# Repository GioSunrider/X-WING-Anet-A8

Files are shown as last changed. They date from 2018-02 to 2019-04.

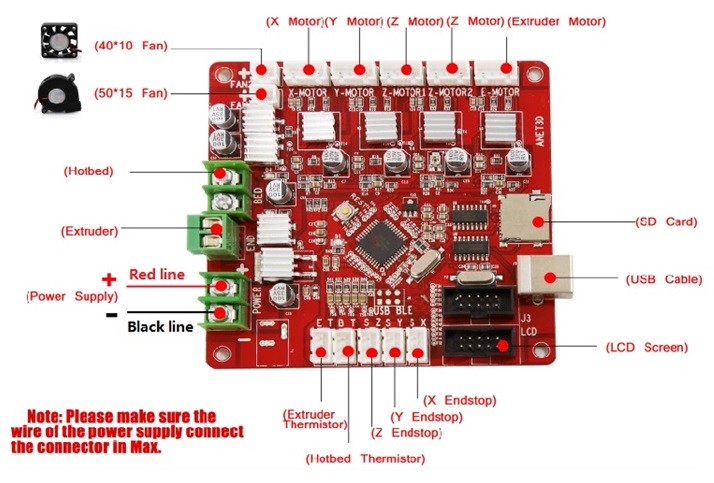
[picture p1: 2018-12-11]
English Instructions/Tool List&other pictures/Mainboard-English.jpg

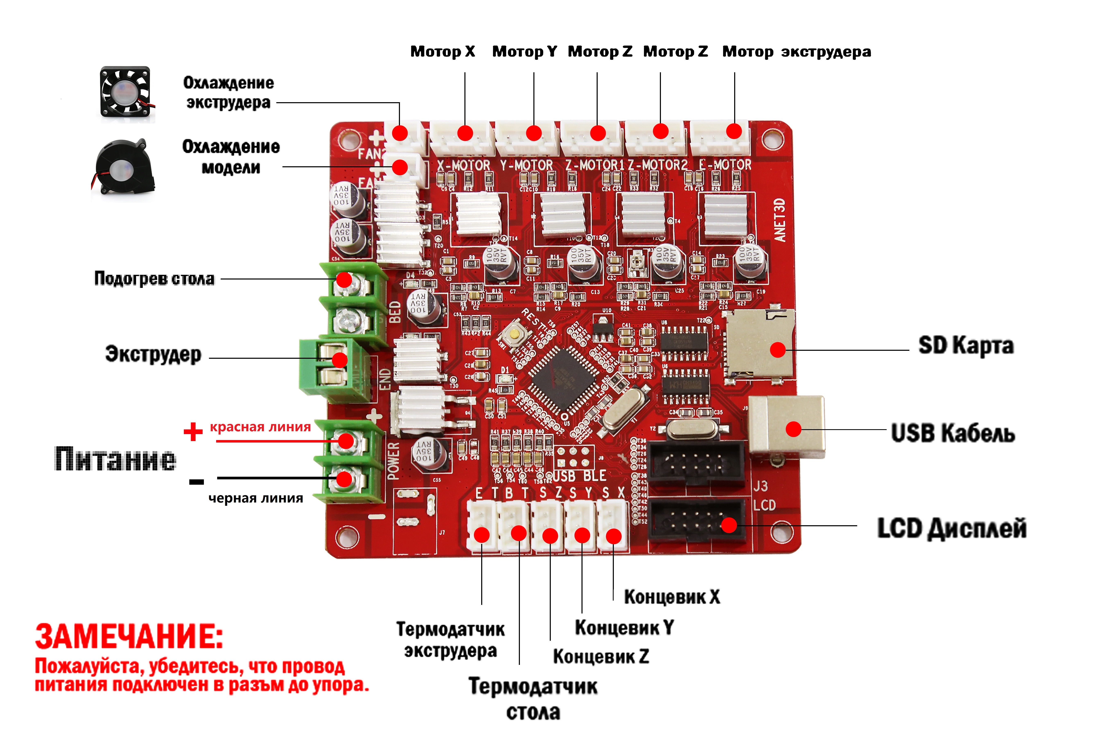
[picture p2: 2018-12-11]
English Instructions/Tool List&other pictures/Mainboard-Russian.jpg

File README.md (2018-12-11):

# X-WING Anet-A8
Proyecto de mejora y documentación de una Anet A8 bautizada como X-WING

En este repositorio se colgara todo lo necesario para su mantenimiento
y mejora de la misma. Asi como sus posibles archivos de configuracion.
______________________________________________________________________________________________

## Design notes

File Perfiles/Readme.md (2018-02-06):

En esta carpeta se encuentran los perfiles de Simplify3D que
se utilizaran en la impresora X-Wing.

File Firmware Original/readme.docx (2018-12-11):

第一步(step 1)

解压avrdudess.zip 文件（ unzip the avrdudess.zip file）

第二步(step 2)

Open avrdudess>avrdudess.exe

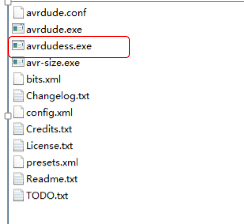
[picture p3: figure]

第三步(step 3)

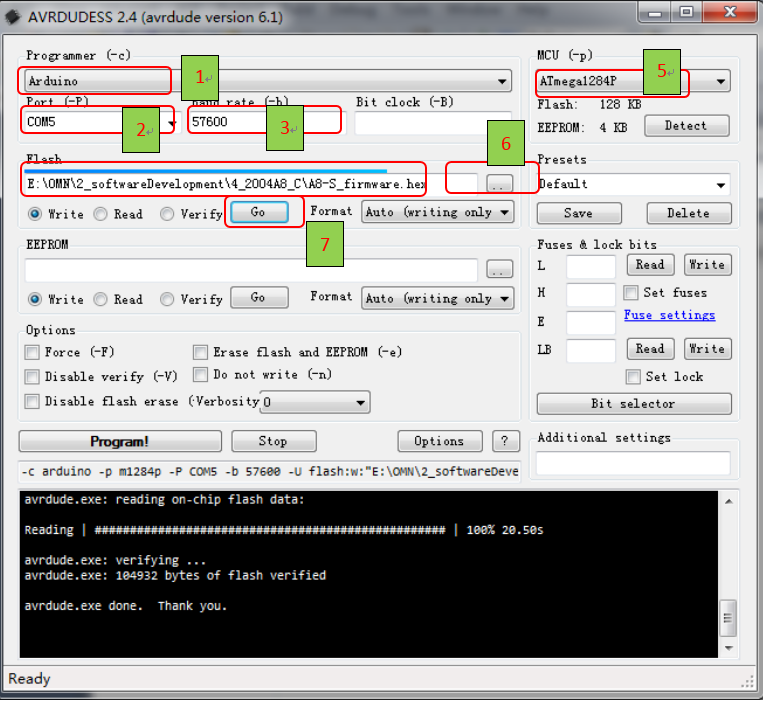
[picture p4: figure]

注意note: 需要查看电脑设备管理器“USB-SERIAL CH340”为准

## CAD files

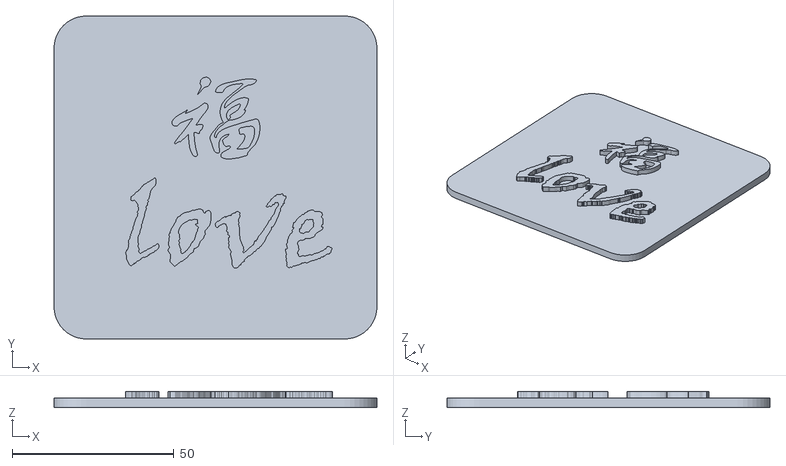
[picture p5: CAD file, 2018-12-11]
English Instructions/Print Model STL/FU.STL
100.0 x 100.0 x 5.00

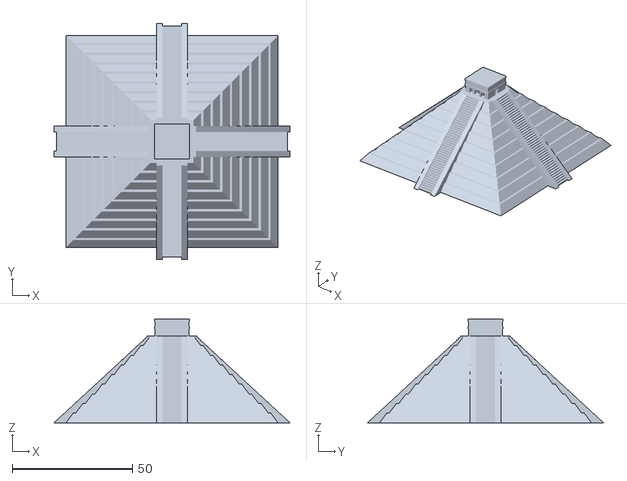
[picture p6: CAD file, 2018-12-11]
English Instructions/Print Model STL/Pyramid.stl
98.0 x 98.0 x 43.0

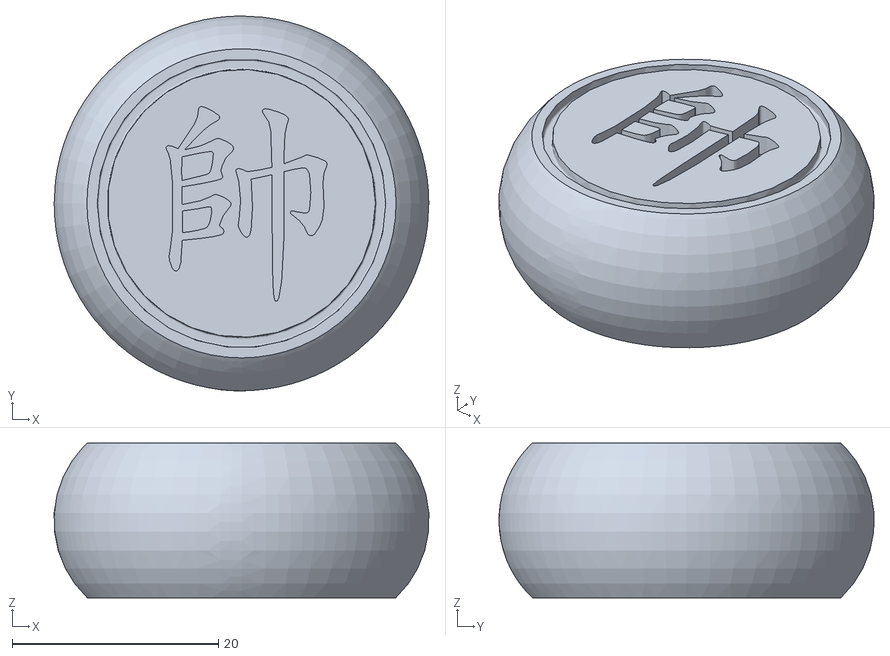
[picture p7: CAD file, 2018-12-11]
English Instructions/Print Model STL/chess.stl
36.4 x 36.4 x 15.0

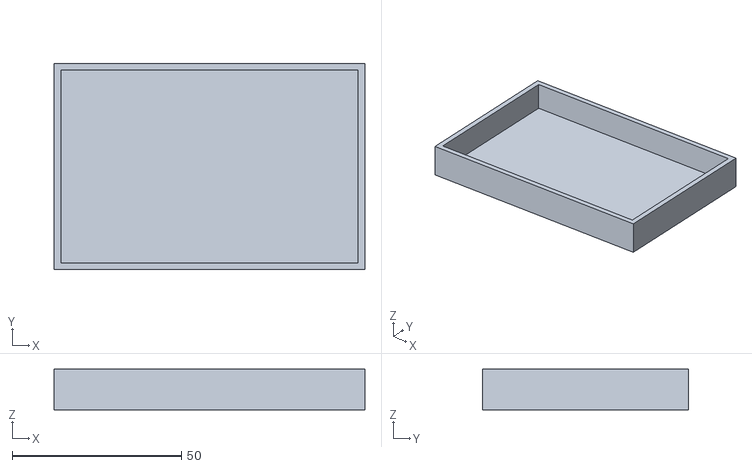
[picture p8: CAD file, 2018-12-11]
English Instructions/Print Model STL/Box.stl
92.0 x 61.0 x 12.0

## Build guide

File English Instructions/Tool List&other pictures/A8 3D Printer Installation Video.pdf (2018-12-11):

## A8 3D Printer Installation Video

Website: https://youtu.be/6W2GuwgPIkI

Title: Anet A8-Updated Installation Video-Part1-Updated date:

2016/12/29

Website: https://youtu.be/J8tX-Kfb1og

Title: Anet A8-Updated Installation Video-Part1-Updated date:

2016/12/29

Website: https://youtu.be/EB5Q3_sJ-Tk

Title: 3D Printer Instruction--Anet 3D Printer A8 Debugging Video (https://www.youtube.com/watch?v=Ml1XGhJF4_E)

Website: https://youtu.be/Ml1XGhJF4_E

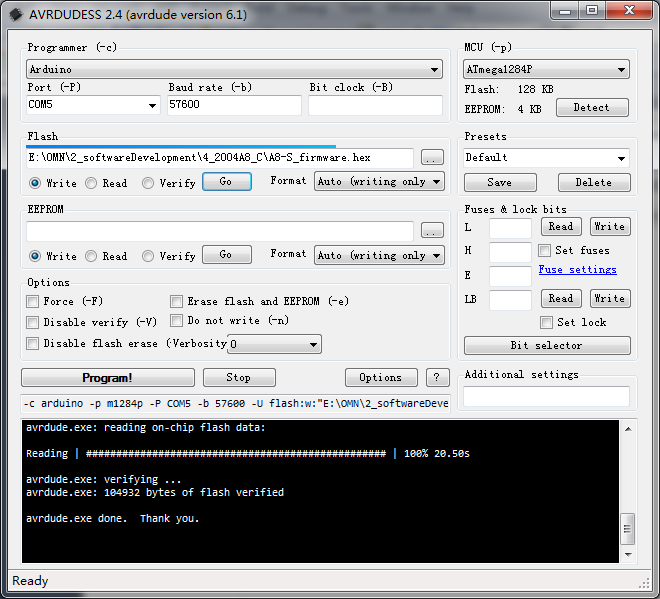
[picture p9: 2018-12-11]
Firmware Original/guide.png

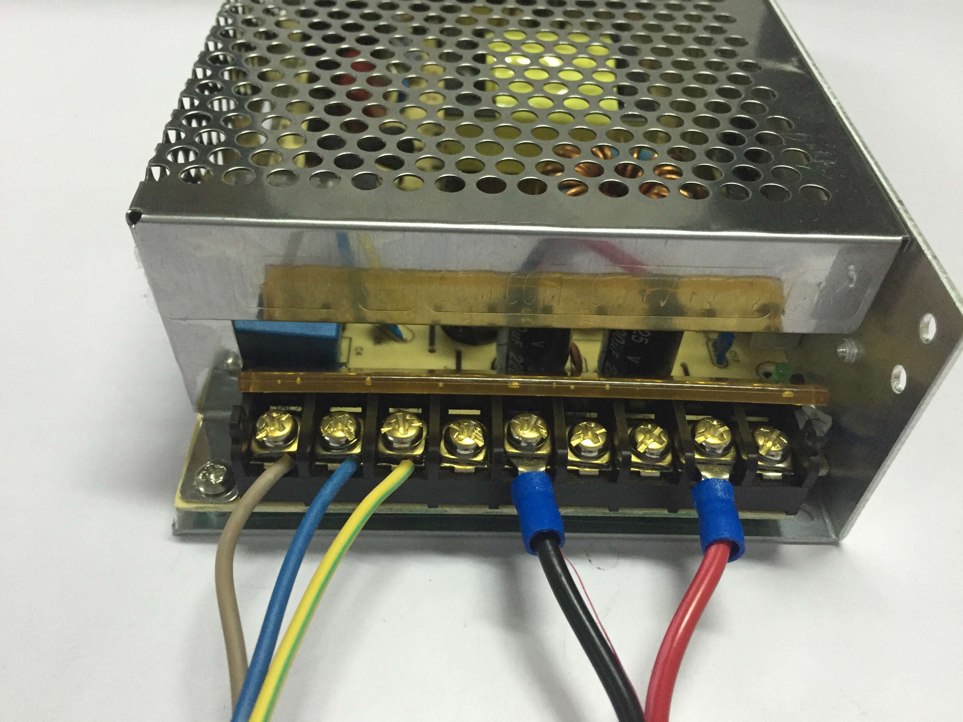
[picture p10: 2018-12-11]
English Instructions/Tool List&other pictures/Power supply wiring.jpg

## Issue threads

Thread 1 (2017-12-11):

Mejora de la H de la cama Caliente

GioSunrider, 2017-12-11:
Se ha perforado los 4 agujeros que sujetan la cama caliente para la eliminacion de la rosca que poseen. De esta manera se ha mejorado la calibracion de la cama caliente. La colocacion es Arandela-Tuerca-Araldela-Muelle. Asi simplemente girando la palometa se podra calibrar la cama.

GioSunrider, 2017-12-12:
Aquí en la foto se ve como es el resultado final.

Closed 2017-12-12.

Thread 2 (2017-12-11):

Investigar Skynet

GioSunrider, 2017-12-11:
Investigar el software Skynet (Marlin modificado) para mejorar la calidad de las Impresiones.

GioSunrider, 2017-12-12:
Se puede obtener el Skynet de [este enlace](https://github.com/SkyNet3D/Marlin/releases) Al parecer tiene una serie de Ventajas y es recomendable actualizar el firmware de la Anet A8/A6 para ganar una serie de mejoras.

Closed 2017-12-12.

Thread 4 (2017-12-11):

Mejora de la Fuente de Alimentación

GioSunrider, 2017-12-11:
Actualmente se esta a la espera de un ventilador, de la marca Sodial comprado en Amazon por 2.12€, que sera intalado para dar ventilacion a la fuente de alimentacion, ya que esta carece de la misma. El ventilador tiene una dimensiones de 90x90x25 mm en CC 12V 0.25A.
Asi mismo tambien se esta a la espera de un conector C14 con un interruptor, para de esta manera, mejorar la conexion y el cableado de la propia fuente, ya que esta dispone de unas conexiones que estan expuestas a un posible contacto por error.

- [x] Colocacion del Interruptor

- [ ] Colocacion del Ventilador

- [ ] Imprimir y Colocar capa del ventilador de la fuente.

GioSunrider, 2017-12-11:
El conector e interruptor son de la marca Sodial, comprado en Amazon por 1.71€. El Enchufe de Corriente Entrada Macho con Interruptor tiene un Fusible de 10A y 250V.

GioSunrider, 2017-12-12:
La pieza que adaptara el interruptor sera [esta](https://www.thingiverse.com/thing:2000523) ya que el interrupto tiene esa forma y se ajusta bien al tamaño de la misma.

GioSunrider, 2017-12-17:
Se ha impreso la pieza para la colocacion del conector-interruptor, ademas se ha soldado las conexiones siguiendo el siguiente modelo encordado en la pagina de mejoras de [Trello](https://trello.com/c/hnF7qBPx/70-interruptor-y-enchufe-para-fuente).

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

Ademas se ha impreso y colocado la pieza de extension de la fuente del sigueinte [enlace](https://www.thingiverse.com/thing:1798604)

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

GioSunrider, 2017-12-19:
Queda unicamente colocar un protector del ventilador, para asi, no pillarte el dedo.

GioSunrider, 2018-01-23:
Como el ventilador se ha instalado en la plca base, se espera a recibir el nuevo ventilador mas pequeño para instalarlo. Luego volveria a quedar una istalacion y un protector para el nnuevo ventilador.

Closed 2018-12-11.

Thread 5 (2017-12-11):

Añadir Pieza al eje Z

GioSunrider, 2017-12-11:
La barra roscada del eje Z se encuentra al aire. Se necesita imprimir [está pieza](https://www.thingiverse.com/thing:2121017) para mejorar el sistema y evitar así oscilaciones del eje Z y posibles temblores.

GioSunrider, 2017-12-12:
Se han impreso e instalado las piezas correspondientes al eje Z. Se adjunta foto de resultado. Ademas se ha añadido a la carpeta `[Parts](https://github.com/GioSunrider/X-WING-Anet-A8/tree/master/Parts)` el correspondiente arhivo de piezas.

Closed 2017-12-12.

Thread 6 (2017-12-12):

Protector Raspberry Pi3 B y Arduino Mega

GioSunrider, 2017-12-12:
- [x] Imprimir [Protector](https://www.thingiverse.com/thing:922740) de Raspberry Pi3 B.

- [x] Imprimir [Protector](https://www.thingiverse.com/thing:1095476) de Arduino Mega.

GioSunrider, 2018-01-14:
Se han impreso satisfactoriamente, e instalado los dos protectores. Se adjunta foto del resultado final.

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

Closed 2018-01-14.

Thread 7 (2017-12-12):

Actualizar Firmware

GioSunrider, 2017-12-12:
- [x] Actualizar firmware a Skynet

Tal y como se ha mencionado en [#2](https://github.com/GioSunrider/X-WING-Anet-A8/issues/2) es recomendable actualizar el firmware.

GioSunrider, 2017-12-12:
Firmware Actualizado. Se añadirá al repositorio.

GioSunrider, 2017-12-15:
Se ha actualizado mediante el IDE de Arduino.

Closed 2017-12-12.

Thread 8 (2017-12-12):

Sujeccion del cristal a 22x22cm

GioSunrider, 2017-12-12:
Tal y como se muestra en el [Trello](https://trello.com/c/6xDvIKiA/234-sujeci%C3%B3n-de-cristal-que-respeta-los-22x22-cm-de-impresi%C3%B3n) es conveniente mantener las medidas de impresion reales. Para ello se imprimiran [estas piezas(x4)](https://www.thingiverse.com/thing:1949142) para asi sujetar mejor el cristal de la cama.

GioSunrider, 2017-12-17:
Se han impreso las primeras 4 piezas para la sujeccion del cristal.

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

Quedaria imprimir la rosca para fijarlas al cristal.

GioSunrider, 2017-12-19:
Se han impreso e instalado las tuercas y los tornillos, ademas de añadirlos a la carpeta [parts](https://github.com/GioSunrider/X-WING-Anet-A8/tree/master/Parts). En la foto se puede ver como ha sido el resultado final.

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

Closed 2017-12-19.

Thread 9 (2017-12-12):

Investigar Octoprint

GioSunrider, 2017-12-12:
Actualmente la impresora es operada manualmente mediante Repetier Host. La idea es que con la Raspberry, crear un servidor de impresion para ella. He oido hablar de Octoprint y Repetier Server. Me he decantado por Octoprnt porque para incorporar una Raspberry parece que da mejor resultado.

GioSunrider, 2017-12-12:
La pagina oficial de [Octoprint](https://octoprint.org/) presenta un manual de instrucciones para su uso e instalacion en su [pagina de descagas](https://octoprint.org/download/).

Closed 2018-12-11.

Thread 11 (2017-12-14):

Reactor MK1 Iron Man

GioSunrider, 2017-12-14:
Imprimir e instalar LEDs para el reactor MK1 de Iron Man para disfraz. [Este enlace](https://www.thingiverse.com/thing:2036876) es el que contiene las piezas para su impresion.

Closed 2018-12-11.

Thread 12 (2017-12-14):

Estabilizador de Camara OpenSAM

GioSunrider, 2017-12-14:
Investigar el proyecto de estabilizador de cámara. En [este enlace](http://opensamofficial.github.io/OpenSAM/) podremos encontrar el proyecto OpenSAM. El primer paso seria la compra de material y la impresión de las piezas.

Closed 2018-12-11.

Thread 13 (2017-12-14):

Colocacion e impresion de piezas para el Cristal de la cama

GioSunrider, 2017-12-14:
Se ha instalado el cristal de la cama (22x22cm) con unas pizas, y se ha procedido a la impresion de [estas piezas](https://www.thingiverse.com/thing:1949142/#files) con las que se fijara el cristal.

Closed 2017-12-14.

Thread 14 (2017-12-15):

Cambo de Repetier a Simplify

GioSunrider, 2017-12-15:
Dado que repetier es un software bastante limitado, me han propuesto el uso de simplify. Realizare el cambio en los proximos dias.

GioSunrider, 2017-12-19:
Se ha instalado el software de Simplify3D, se esta cacharreando un poco con el y configurando los parametros ideales para la impresora.

GioSunrider, 2018-01-14:
Se han impreso las primeras piezas con Simplify con un buen resultado aunque todavia faltan unos cuantos ajusten que dejen mejor las piezas.

GioSunrider, 2018-01-14:
Configuración optima del Simplify correcta, posteriormente se subirá el perfil de impresión. En [#6](https://github.com/GioSunrider/X-WING-Anet-A8/issues/6) se pueden ver los resultados de este perfil, ya que ambos protectores se han impreso con el mismo.

Closed 2018-01-14.

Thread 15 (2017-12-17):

Base de Goma EVA

GioSunrider, 2017-12-17:
Se ha colocado la impresora sobre una base de Goma EVA para reducir las vibraciones, asi como evitar posibles deslizamientos del acrilico sobre la mesa, ya que este resbala un poco sobre madera.

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

Closed 2017-12-17.

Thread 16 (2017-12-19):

Soldado de la Cama Caliente

GioSunrider, 2017-12-19:
Se han soldado los cables de la cama caliente, retirando el conector anteriormente colocado.

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

Para ello se ha retirado y soldado lo cables directamente a la cama. El hecho de hacer este cambio no es otro que la proteccion contra posibles incendios, ya que por aqui pasa bastante ampreaje y el conector que se encuentra puede sufrir graves daños. En la foto se puede obserbar el resultado final.

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

Closed 2017-12-19.

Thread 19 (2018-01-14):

Ventilador de Placa Base

GioSunrider, 2018-01-14:
Añadir una [tapa](https://www.thingiverse.com/thing:1803120) en la que se instalara el ventilador que servira de refrigeracion de la placa base para evitar sobrecalentamientos y prevenir posibles incendios.

GioSunrider, 2018-01-14:
El ventilador ha sido comprado por [Amazon](https://www.amazon.es/gp/product/B00X3KGB4S/ref=oh_aui_detailpage_o02_s00?ie=UTF8&psc=1).

GioSunrider, 2018-01-18:
Se ha añadido a la carpeta de [Parts](https://github.com/GioSunrider/X-WING-Anet-A8/tree/master/Parts) las partes en las que ira colocado el Ventilador. Se ha decido que el ventilador que actualmente se encuentra en la fuente de alimentacion como se indico su instalacion en [#4](https://github.com/GioSunrider/X-WING-Anet-A8/issues/4), pase a ser el ventilador de la placa base, y el ventilador que recibire, pase al de la fuente de alimentacion. Ya que esta no necesita tanta ventilacion.

GioSunrider, 2018-01-23:
Se ha instalado el ventilador en la placa base. Se adjunta foto del resultado final.

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

Closed 2018-01-23.

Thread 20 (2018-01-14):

Mosfet cama caliente

GioSunrider, 2018-01-14:
Se ha procedido a la compra por [Amazon](https://www.amazon.es/gp/product/B0714JXQT7/ref=oh_aui_detailpage_o00_s00?ie=UTF8&psc=1) de un MOSFET que se instalara como prevención de incendios y sus conexiones seran mostradas en el siguiente esquema.

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

Se necesitara imprimir un soporte para la colocación del mismo.

Closed 2018-12-11.

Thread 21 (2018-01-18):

Mejora de la estabilidad de la estructura

GioSunrider, 2018-01-18:
Tal y como se muestra en el [Trello](url) se van a imprimir e instalar unas piezas referidas como mejora de la estabilidad.

- [x] [Estabilidad tasera](https://trello.com/c/oBT24dLE/51-estabilidad-refuerzos-y-anclajes)

- [ ] [Estabilidad delantera](https://www.thingiverse.com/thing:1672959)

- [x] [Estabilizad base](https://www.thingiverse.com/thing:2067872)

- [ ] [Refuerzo entre base y marco](https://www.thingiverse.com/thing:1232870) Para este, se compraran unas barras roscadas M8 para reforzar la estructura

Se han añadido a su vez las piezas a la carpeta [Parts](https://github.com/GioSunrider/X-WING-Anet-A8/tree/master/Parts)

GioSunrider, 2018-01-23:
Se han impreso e instalado algunas de las piezas, tambien se han añadido las piezas a la carpeta [Parts](https://github.com/GioSunrider/X-WING-Anet-A8/tree/master/Parts). Se adjunta foto del resultado final.

Estabilidad de la base.
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

Estabilidad Trasera.
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

Asi mismo, la pieza de T, aunque impresa, no haria falta debido a que entra en conflicto con la posicion de las piezas de la estabilidad trasera.

Closed 2018-12-11.

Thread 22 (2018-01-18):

Tensor del Eje Y y Mejora de Sujeccion de la Correa del Eje X

GioSunrider, 2018-01-18:
Sen han impreso y añadido a la carpeta de [Parts](https://github.com/GioSunrider/X-WING-Anet-A8/tree/master/Parts) las piezas correspondientes al tensor del eje Y y la fijacion trasera de la correa del eje X.
Ambas han sido sacadas de los siguientes enlaces.
[Tensor Eje Y](https://www.thingiverse.com/thing:1959208)
[Sujeccion Correa Eje X](https://www.thingiverse.com/thing:2584156)

GioSunrider, 2018-01-23:
Tambien se ha impreso un [Tensor del Eje X](https://www.thingiverse.com/thing:2507473/#files)

GioSunrider, 2018-01-23:
Se han instalado todas las piezas. Se adjunta foto del resultado final.

Tensor del Eje Y.
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

Tensor del Eje X.
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

Sujeccion Correa del Eje X.
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

Closed 2018-01-23.

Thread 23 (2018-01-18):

Soporte de Filamento

GioSunrider, 2018-01-18:
Se va a imprimir una ampliación del soporte del filamento para  dar cabida a dos o tres bobinas dependiendo del tamaño. La pieza ha sido añadida a la carpeta [Parts](https://github.com/GioSunrider/X-WING-Anet-A8/tree/master/Parts). Ademas se necesita ampliar la barra roscada que actualmente se encuentra. Y por ultimo añadir un soporte para que la bobina apoye en el, y no en la barra.
La pieza es [esta](https://www.thingiverse.com/thing:2251232/#files).
Y el soporte es necesario buscarlo todavia.

Closed 2018-12-11.

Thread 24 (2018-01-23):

Correcion de las Llamadas "Olas" en las piezas

GioSunrider, 2018-01-23:
Despues de imprimir un sin fin de piezas, nos hemos dado cuentas que debido a la acceleracion de los motores las piezas impresas salian con este desperfecto. Se ha modificado Skynet para corregir este error. Se procedera a subier el nuevo Configuration.h al codigo. Asi mismo, se subira el perfil utilizado con el software de Simplify3D que tambien ha sido modificado.

Closed 2018-12-11.

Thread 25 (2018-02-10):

PLA 1.75 Smartfil

GioSunrider, 2018-02-10:
Actualmente se encuentran en uso tres bobinas de Smartfil compradas por 65.26€ en [3dprinters-shop](https://www.3dprinters-shop.com/es/). Las bobinas corresponden a los colores CHLOROPHYLL, TRUE BLACK y IVORY BLANCO.

Closed 2018-12-11.

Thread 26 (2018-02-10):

Adaptador para filamento flexible.

GioSunrider, 2018-02-10:
Se ha impreso e instalado el adaptador del extrusor MK8 para la utilizacion de filamento flexible, tal y como se muestra en el [Trello](https://trello.com/c/BiTMdPDt/37-adaptador-para-filaflex).

Closed 2018-02-10.

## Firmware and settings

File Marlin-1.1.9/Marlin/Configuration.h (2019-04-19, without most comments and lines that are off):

#define CONFIGURATION_H
#define CONFIGURATION_H_VERSION 010109
#define STRING_CONFIG_H_AUTHOR "GioSunrider " // Who made the changes. //GS
#define SHOW_BOOTSCREEN
#define STRING_SPLASH_LINE1 "X-Wing Loading "             // will be shown during bootup in line 1 //GS
#define STRING_SPLASH_LINE2 "Marlin " SHORT_BUILD_VERSION // will be shown during bootup in line 2 //GS
#define SERIAL_PORT 0
#define BAUDRATE 115200 //GS
  #define MOTHERBOARD BOARD_ANET_10 //GS
#define CUSTOM_MACHINE_NAME "X-Wing " //GS
#define MACHINE_UUID "ff413aeb-bf85-48af-abdd-d7e8c9626c0f" //GS
#define EXTRUDERS 1
#define DEFAULT_NOMINAL_FILAMENT_DIA 1.75 //GS
#define POWER_SUPPLY 0
#define TEMP_SENSOR_0 5
#define TEMP_SENSOR_1 0
#define TEMP_SENSOR_2 0
#define TEMP_SENSOR_3 0
#define TEMP_SENSOR_4 0
#define TEMP_SENSOR_BED 5
#define TEMP_SENSOR_CHAMBER 0
#define DUMMY_THERMISTOR_998_VALUE 25
#define DUMMY_THERMISTOR_999_VALUE 100
#define MAX_REDUNDANT_TEMP_SENSOR_DIFF 10
#define TEMP_RESIDENCY_TIME 6   // (seconds)
#define TEMP_HYSTERESIS 3       // (degC) range of +/- temperatures considered "close" to the target one
#define TEMP_WINDOW     1       // (degC) Window around target to start the residency timer x degC early.
#define TEMP_BED_RESIDENCY_TIME 6   // (seconds)
#define TEMP_BED_HYSTERESIS 3       // (degC) range of +/- temperatures considered "close" to the target one
#define TEMP_BED_WINDOW     1       // (degC) Window around target to start the residency timer x degC early.
#define HEATER_0_MINTEMP 5
#define HEATER_1_MINTEMP 5
#define HEATER_2_MINTEMP 5
#define HEATER_3_MINTEMP 5
#define HEATER_4_MINTEMP 5
#define BED_MINTEMP 5
#define HEATER_0_MAXTEMP 275
#define HEATER_1_MAXTEMP 275
#define HEATER_2_MAXTEMP 275
#define HEATER_3_MAXTEMP 275
#define HEATER_4_MAXTEMP 275
#define BED_MAXTEMP 130
#define PIDTEMP
#define BANG_MAX 255     // Limits current to nozzle while in bang-bang mode; 255=full current
#define PID_MAX BANG_MAX // Limits current to nozzle while PID is active (see PID_FUNCTIONAL_RANGE below); 255=full current
#define PID_K1 0.95      // Smoothing factor within any PID loop
  #define PID_FUNCTIONAL_RANGE 15 // If the temperature difference between the target temperature and the actual temperature
  #define DEFAULT_Kp 21.0 //GS
  #define DEFAULT_Ki 1.25 //GS
  #define DEFAULT_Kd 86.0 //GS
#define BED_LIMIT_SWITCHING
#define MAX_BED_POWER 255 // limits duty cycle to bed; 255=full current
#define PREVENT_COLD_EXTRUSION
#define EXTRUDE_MINTEMP 160  // 160 guards against false tripping when the extruder fan kicks on.
#define PREVENT_LENGTHY_EXTRUDE
#define EXTRUDE_MAXLENGTH 200
#define THERMAL_PROTECTION_HOTENDS // Enable thermal protection for all extruders
#define THERMAL_PROTECTION_BED     // Enable thermal protection for the heated bed
#define USE_XMIN_PLUG
#define USE_YMIN_PLUG
#define USE_ZMIN_PLUG
#define ENDSTOPPULLUPS
#define X_MIN_ENDSTOP_INVERTING true  // set to true to invert the logic of the endstop.
#define Y_MIN_ENDSTOP_INVERTING true  // set to true to invert the logic of the endstop.
#define Z_MIN_ENDSTOP_INVERTING true  // set to true to invert the logic of the endstop.
#define X_MAX_ENDSTOP_INVERTING false // set to true to invert the logic of the endstop.
#define Y_MAX_ENDSTOP_INVERTING false // set to true to invert the logic of the endstop.
#define Z_MAX_ENDSTOP_INVERTING false // set to true to invert the logic of the endstop.
#define Z_MIN_PROBE_ENDSTOP_INVERTING true  // set to true to invert the logic of the probe.
#define ENDSTOP_INTERRUPTS_FEATURE
#define DEFAULT_AXIS_STEPS_PER_UNIT   { 100, 100, 400, 300 } //GS
#define DEFAULT_MAX_FEEDRATE          { 400, 400, 8, 150 } //GS
#define DEFAULT_MAX_ACCELERATION      { 2000, 2000, 100, 10000 } //GS
#define DEFAULT_ACCELERATION          300     // X, Y, Z and E acceleration for printing moves  //GS
#define DEFAULT_RETRACT_ACCELERATION  1000    // E acceleration for retracts  //GS
#define DEFAULT_TRAVEL_ACCELERATION   800    // X, Y, Z acceleration for travel (non printing) moves //GS
#define DEFAULT_XJERK                 10.0 //GS
#define DEFAULT_YJERK                 10.0 //GS
#define DEFAULT_ZJERK                  0.3  //GS
#define DEFAULT_EJERK                 15.0  //GS
#define S_CURVE_ACCELERATION
#define Z_MIN_PROBE_USES_Z_MIN_ENDSTOP_PIN
#define X_PROBE_OFFSET_FROM_EXTRUDER -25 //GS  // X offset: -left  +right  [of the nozzle]
#define Y_PROBE_OFFSET_FROM_EXTRUDER 5   //GS  // Y offset: -front +behind [the nozzle]
#define Z_PROBE_OFFSET_FROM_EXTRUDER 0   //GS  // Z offset: -below +above  [the nozzle]
#define MIN_PROBE_EDGE 10
#define XY_PROBE_SPEED 6000
#define Z_PROBE_SPEED_FAST HOMING_FEEDRATE_Z
#define Z_PROBE_SPEED_SLOW (Z_PROBE_SPEED_FAST / 2)
#define Z_CLEARANCE_DEPLOY_PROBE   10 // Z Clearance for Deploy/Stow
#define Z_CLEARANCE_BETWEEN_PROBES  5 // Z Clearance between probe points
#define Z_CLEARANCE_MULTI_PROBE     5 // Z Clearance between multiple probes
#define Z_PROBE_LOW_POINT          -2 // Farthest distance below the trigger-point to go before stopping
#define Z_PROBE_OFFSET_RANGE_MIN -20
#define Z_PROBE_OFFSET_RANGE_MAX 20
#define X_ENABLE_ON 0
#define Y_ENABLE_ON 0
#define Z_ENABLE_ON 0
#define E_ENABLE_ON 0 // For all extruders
#define DISABLE_X false
#define DISABLE_Y false
#define DISABLE_Z false
#define DISABLE_E false // For all extruders
#define DISABLE_INACTIVE_EXTRUDER true // Keep only the active extruder enabled.
#define INVERT_X_DIR false
#define INVERT_Y_DIR false
#define INVERT_Z_DIR true
#define INVERT_E0_DIR false
#define INVERT_E1_DIR false
#define INVERT_E2_DIR false
#define INVERT_E3_DIR false
#define INVERT_E4_DIR false
#define X_HOME_DIR -1
#define Y_HOME_DIR -1
#define Z_HOME_DIR -1
#define X_BED_SIZE 220  //GS
#define Y_BED_SIZE 220  //GS
#define X_MIN_POS -13   //GS
#define Y_MIN_POS -13   //GS
#define Z_MIN_POS 0     //GS
#define X_MAX_POS 250   //GS
#define Y_MAX_POS 250   //GS
#define Z_MAX_POS 235   //GS
#define MIN_SOFTWARE_ENDSTOPS
  #define MIN_SOFTWARE_ENDSTOP_X
  #define MIN_SOFTWARE_ENDSTOP_Y
  #define MIN_SOFTWARE_ENDSTOP_Z
#define MAX_SOFTWARE_ENDSTOPS
  #define MAX_SOFTWARE_ENDSTOP_X
  #define MAX_SOFTWARE_ENDSTOP_Y
  #define MAX_SOFTWARE_ENDSTOP_Z
#define HOMING_FEEDRATE_XY (100*60)
#define HOMING_FEEDRATE_Z  (4*60)
#define EEPROM_SETTINGS   // Enable for M500 and M501 commands
#define EEPROM_CHITCHAT   // Give feedback on EEPROM commands. Disable to save PROGMEM.
#define BUSY_WHILE_HEATING            // Some hosts require "busy" messages even during heating
#define PREHEAT_1_TEMP_HOTEND 205 //GS
#define PREHEAT_1_TEMP_BED     55 //GS
#define PREHEAT_1_FAN_SPEED     0 // Value from 0 to 255
#define PREHEAT_2_TEMP_HOTEND 240 //GS
#define PREHEAT_2_TEMP_BED     90 //GS
#define PREHEAT_2_FAN_SPEED     0 // Value from 0 to 255
#define PREHEAT_3_TEMP_HOTEND 210 //GS
#define PREHEAT_3_TEMP_BED     40 //GS
#define PREHEAT_3_FAN_SPEED     0 // Value from 0 to 255
#define PREHEAT_4_TEMP_HOTEND 230 //GS
#define PREHEAT_4_TEMP_BED    100 //GS
#define PREHEAT_4_FAN_SPEED     0 // Value from 0 to 255
#define NOZZLE_PARK_FEATURE //GS
  #define NOZZLE_PARK_POINT { (X_MIN_POS + 10), (Y_MAX_POS - 10), 30 }
  #define NOZZLE_PARK_XY_FEEDRATE 100   // X and Y axes feedrate in mm/s (also used for delta printers Z axis)
  #define NOZZLE_PARK_Z_FEEDRATE 5      // Z axis feedrate in mm/s (not used for delta printers)
#define PRINTJOB_TIMER_AUTOSTART
#define LCD_LANGUAGE es //GS
#define DISPLAY_CHARSET_HD44780 JAPANESE
#define SDSUPPORT
#define ZONESTAR_LCD              // Requires ADC_KEYPAD_PIN to be assigned to an analog pin.
#define SOFT_PWM_SCALE 0
#define SERVO_DELAY { 300 }

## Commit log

2018-01-25 Perfil de Simplify3D
2018-04-14 Marlin Actualizado - Anet A8
    [Configuration.h, Configuration_adv.h]

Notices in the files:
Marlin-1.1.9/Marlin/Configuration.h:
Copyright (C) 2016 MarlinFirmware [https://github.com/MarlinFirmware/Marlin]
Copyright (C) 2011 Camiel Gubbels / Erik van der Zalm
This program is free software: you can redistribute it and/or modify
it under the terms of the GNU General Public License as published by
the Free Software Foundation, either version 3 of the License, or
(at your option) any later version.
